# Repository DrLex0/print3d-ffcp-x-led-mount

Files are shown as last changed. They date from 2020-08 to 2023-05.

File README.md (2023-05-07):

# 5 mm LED mount clip for 8 mm X axis
*A clip to mount a 5 mm LED on the 8 mm X axis of the FlashForge Creator Pro or similar 3D printers (formerly thing:1790072)*

### License
[Creative Commons - Attribution](https://creativecommons.org/licenses/by/4.0/)

### Gallery

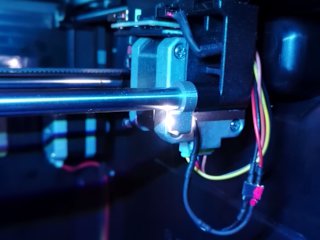
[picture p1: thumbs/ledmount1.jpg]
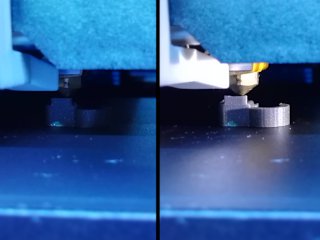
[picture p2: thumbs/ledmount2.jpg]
Photo 2 - before & after
[🔎](images/ledmount1.jpg) [🔎](images/ledmount2.jpg)

## Description and Instructions

This is a basic clip that allows to mount a single 5 mm LED onto the X axis of a FlashForge Creator Pro, Dreamer, or similar printer (anything vaguely looking like a Replicator probably). When using a high performance narrow-beam LED like a Nichia NSPW500GS-K1 driven at 20 mA, this can add a nice amount of sideways lighting that moves together with the Y position. (See the second photo for a “before vs. after.”) The LED is aimed such that it will provide optimal lighting for the middle X position.

This is especially useful if you have mounted something that blocks the light from the printer's own LED strip, like my [dual fan duct](https://github.com/DrLex0/print3d-ffcp-dual-cooling-duct). Now I no longer need to check with a flashlight whether the first layer is OK or not.

### Printing

I print these at 0.1 mm layers, infill doesn't really matter.

Things tend to get pretty warm near the X stepper, therefore I would recommend ABS for maximum heat resistance. PETG is probably also OK.
A brim or raft may be needed.
Whatever material you print this in, you will probably need to blast it with the cooling fan at full power even if it is ABS, because this is a small part and the layers might not cool quickly enough on their own.

If the LED doesn't fit, use a 5 mm drill to ream the hole.

### Installing

You will need to route some additional wires coming from the base of the printer. You can attach them to the existing cables that go to the X stepper. I advise against using zip-ties for this, because they can induce strain that may cause the wires to develop a bad connection, which is especially problematic if a wire driving the stepper motor becomes damaged. If you do use zip-ties, do not tighten them all the way. Better is to avoid zip-ties altogether and instead, either wrap the extra cable around the existing ones, or use some soft flexible ties or perhaps simple adhesive tape.

**Do not** attempt to skimp on circuitry or wiring by powering the LED from any point on the main board or the 5 V line of an endstop. You may exceed the maximum current draw of a circuit, and cause permanent damage to the main board.

Your best and safest option to power the LED is to hook up a completely independent supply to the mains line (you can piggyback on the screw connectors of the PSU, which will also cause LEDs to be switched together with the rest of the printer). This is what I initially did, it eliminates any risk of overloading the PSU or blowing up something unprotected on the rather expensive main board. After I had installed a Raspberry Pi for my [variable fan speed controller](https://github.com/DrLex0/MightyVariableFan), I simply tapped into one of the 5 V pins of the Pi's GPIO pin header. (You could take this a step further by actually making the LED switchable through a GPIO pin, but then you should not drive the LED directly from the pin but do it through a MOSFET board of some kind.)

A good alternative is a current source (an LED driver) that efficiently produces a fixed 20 or 25 mA current from the 24 V input of the main power supply. Do not attempt to use a plain series resistor to bring down the 24 V to the ≈3.2 V needed for the LED: not only will it waste about 0.4 W, it will also most likely go up in smoke.

## Updates

### 2016/09/25
First published on Thingiverse.

### 2017/07/03: v2
Added v2 version which is aimed slightly lower so it lights up more of the print. This is also a tad longer so it has less risk of colliding with modded carriages, and the overall shape has been made such that it is less likely to warp when printed in ABS.

### 2020/08/16: v3
Migrated to GitHub. Extended the little cover such that it better shields your eyes from direct light of the LED.

## Tags
`FFCP`, `FFCPRo`, `Flashforge_Creator_PRO`, `FlashForge_Dreamer`, `LED`, `light`, `lighting`, `mount`, `replicator`

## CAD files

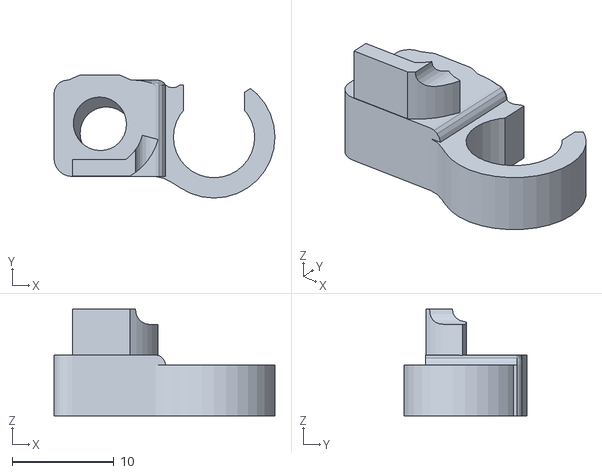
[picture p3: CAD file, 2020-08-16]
FFCP-LEDmount-right.stl
21.8 x 12.1 x 10.5

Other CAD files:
FFCP-LEDmount-left.stl
